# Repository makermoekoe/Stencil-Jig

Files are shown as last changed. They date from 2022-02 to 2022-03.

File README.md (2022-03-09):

# Stencil-Jig

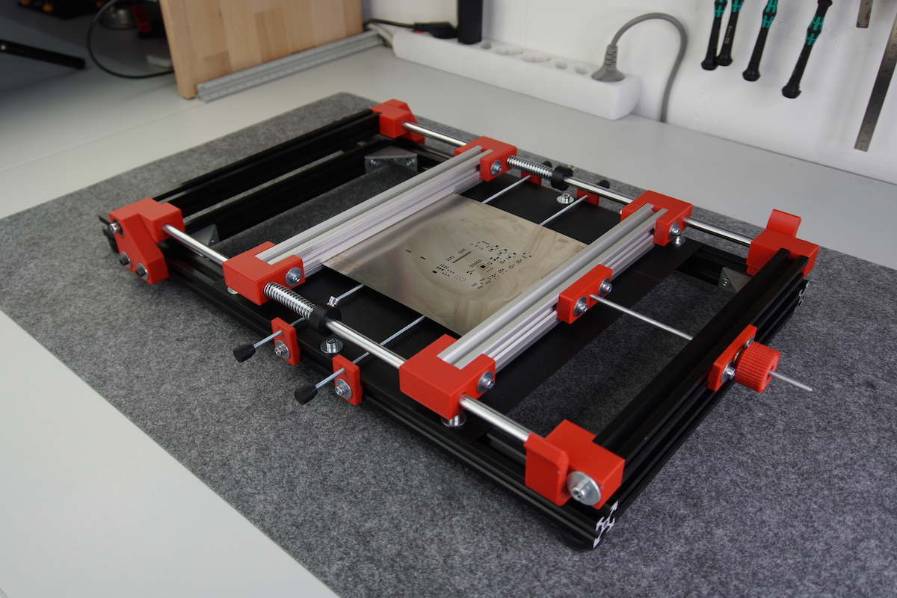
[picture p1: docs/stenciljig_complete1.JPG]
</a>
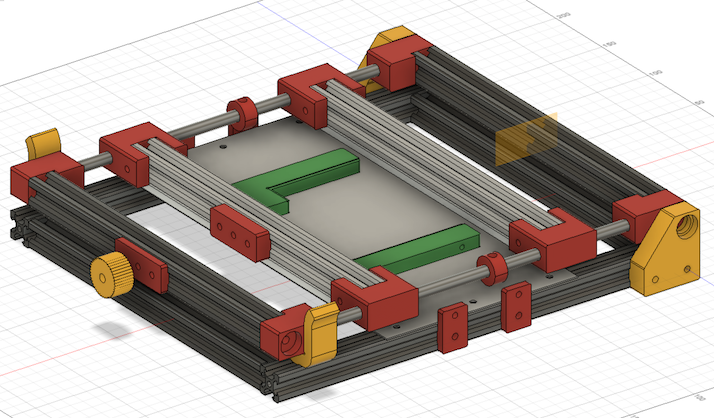
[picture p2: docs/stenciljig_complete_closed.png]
</a>
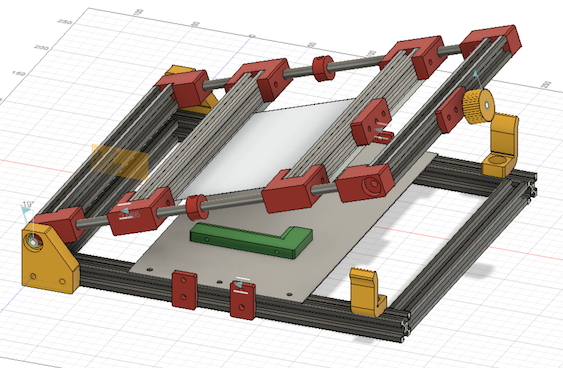
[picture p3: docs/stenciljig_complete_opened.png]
</a>

The Stencil-Jig is a simple DIY machine for PCB stenciling built with the Openbuilds v-slot system. Dealing with those stencils is always tricky, because they have to be aligned perfectly to get great soldering results. So far, I was always using these stencils with spare PCBs around the project PCB which are fixed in position with tape. As I am using these stencils quite often in the last time I was thinking about creating a simple jig for it - and here it is.

The stencils can be clamped into the Stencil-Jig with the inner v-slot extrusions. With all the adjustment screws on the sides and the front, the PCB and the stencil can be aligned easily to fit each other (at least this is the plan). The PCB holders are not yet the best option but they are working for now. If you have other ideas of how the PCB alignment could be done better then please let me know!

These built is inspired by two other DIY designs of Stencil printers/jigs/machines:

- Valera Perinski: https://www.thingiverse.com/thing:3429201
- Dengler Mechatronik: https://dengler-mechatronik.de/?p=560

## Assembling

I've created a detailed video about the assembly process of the StencilJig. There are notes in the video as well.

- video link here

## Extrusions

V-slot extrusions are probably not necessary here, because the v-bearings are not used. Nevertheless I have chosen them because of the availability and v-style of the slots in order to align 3D-printed parts with only one screw.

For this project you will need 5x 500mm 2020 extrusions which will be cut into these dimensions:

- 6x 250mm; width of the jig (it is probably 249,5mm, because I have just cut a 500mm extrusion in half)
- 2x 500mm; length of the jig (can be shortened later, so I leaved it as it is first)

## What to print

For the complete machine, as it is seen in the picture below, you'll need the following parts to be printed:

- 1x hinge_left.stl
- 1x hinge_right.stl
- 4x slide_mount.stl
- 4x slider.stl
- 2x slide_stopper.stl
- 2x alignment_guide.stl
- 1x screwstop_m4_incl.stl
- 1x screwstop_m4_knob.stl
- 1x knob_m4.stl
- 4x screwstop.stl
- 4x knob_m3.stl
- 1x pcb_mount_edge_1_6mm.stl
- 1x pcb_mount_straight_1_6mm.stl

## What you need

Except the 3D printed parts and the extrusions listed above you will also need the following parts:

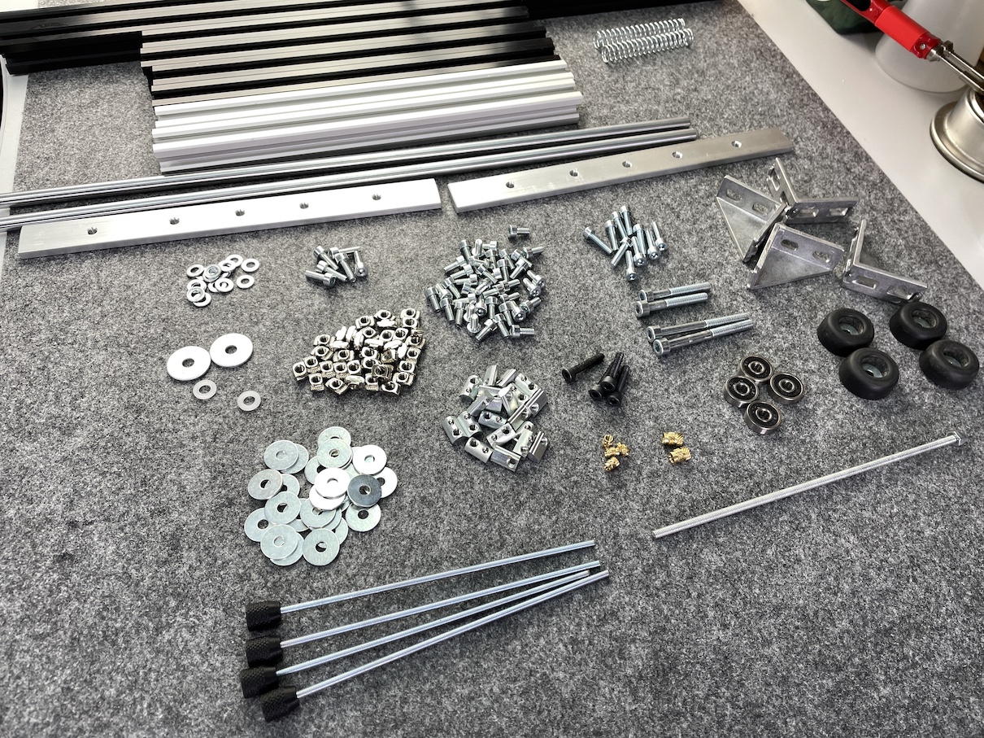
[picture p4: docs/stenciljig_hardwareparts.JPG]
</a>

- 2x 8mm stainless steel rod (length = length of the jig - 40mm)
- 4x 625RS bearings (16x5x5mm)
- 2x strong springs for the 8mm rod
- 4x M3 threaded rod ~100mm
- 1x M4 threaded rod ~100mm
- 1x steel plate 1mm (~290mmx250mm)
- 2x aluminium extrusion 5x20x220mm
- 4x extrusion corner 4040
- 4x M3 threaded insert
- 3x M4 threaded insert
- 40x M4 screw DIN 912 8mm
- 6x M4 screw DIN 912 12mm
- 10x M4 screw DIN 912 20mm
- 4x M4 screw DIN 912 25mm
- 2x M5 screw DIN 912 50mm
- 2x M5 screw DIN 912 30mm
- 60x M4 extrusion nuts
- 1x M4 self-locking nut
- Xx washers 4,3mm x 15mm
- 4x washers 5,3mm x 15mm
- 2x washers 5,3mm x 10mm polyamid
- (4x machine foots)

## Alignment guides

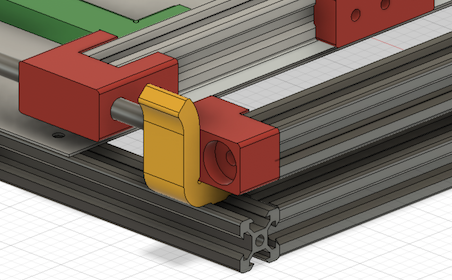
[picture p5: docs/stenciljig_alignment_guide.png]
</a>

The alignment guides are there to hold the upper part of the jig (including the stencil) during the stenceling process in place, so that it doesn't move to the left or right.

## TODOs

- Alignment guide: This part should be modified with two magnets facing against each other so that the top of jig will be pushed down once inserted in the alignment guide. This will keep the stencil down.
- The PCB holders should be optimized. At least they should be wider and on the same high as the PCB so that the stencil won't bent.
- Springs should be stronger. Or exchanging the springs with a tightener (knob as in the front) on the back?!

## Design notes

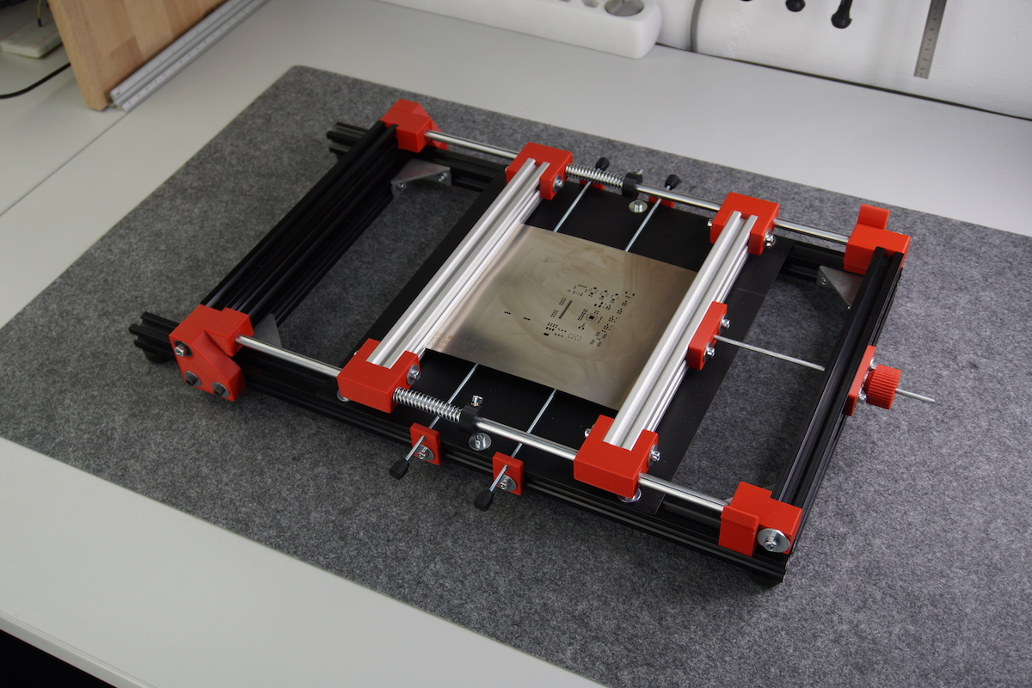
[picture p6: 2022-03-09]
docs/stenciljig_complete2.JPG

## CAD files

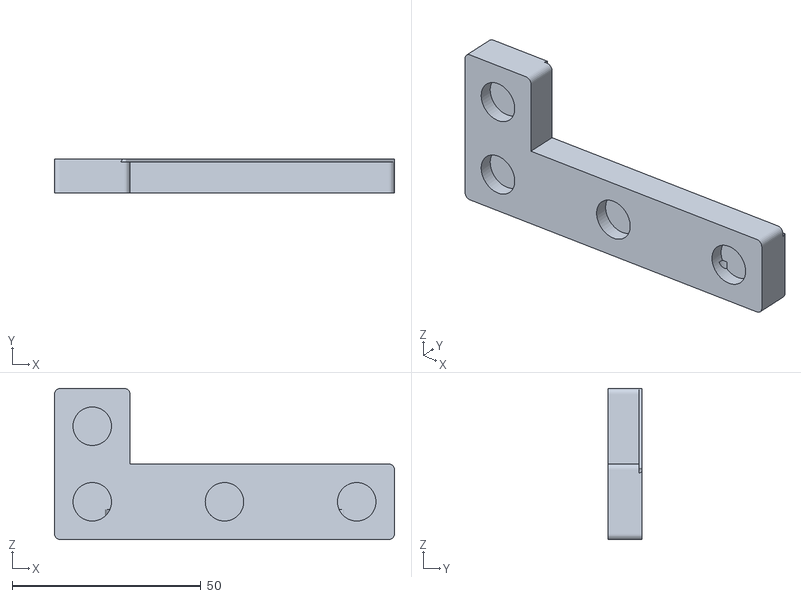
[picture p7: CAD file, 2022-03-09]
3d_files/pcb_mount_edge_1_6mm.stl
90.0 x 9.00 x 40.0

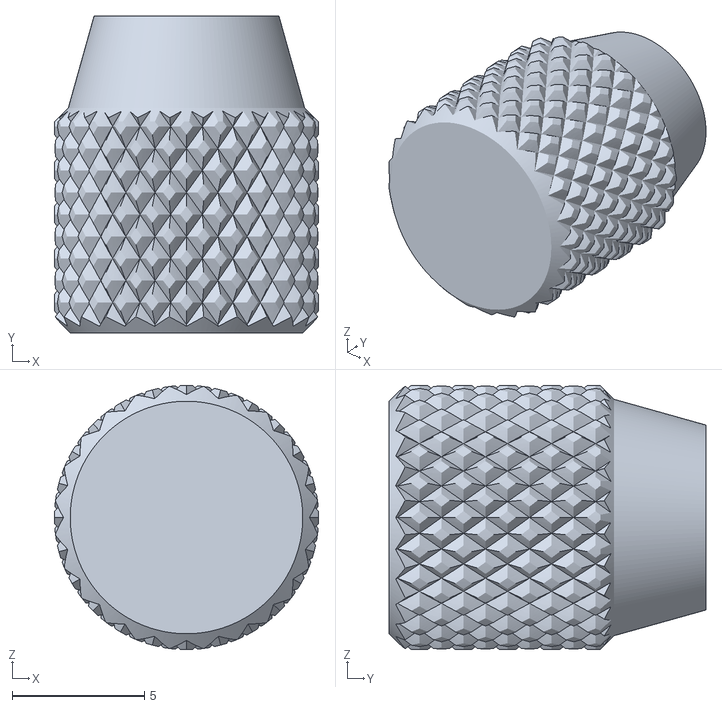
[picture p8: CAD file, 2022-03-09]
3d_files/knob_m3.stl
10.0 x 12.0 x 10.0

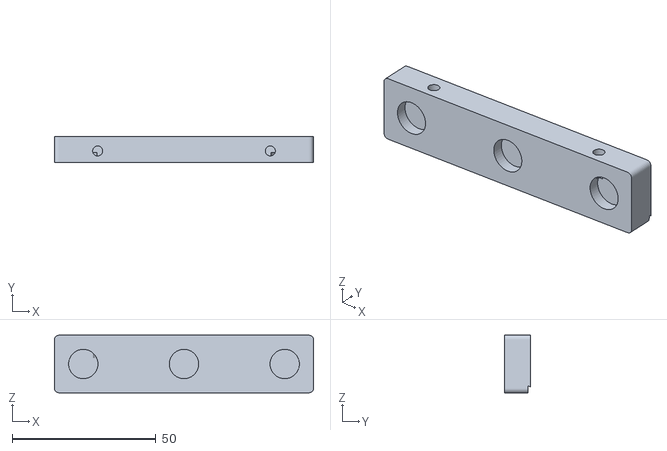
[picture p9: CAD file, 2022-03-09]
3d_files/pcb_mount_straight_1_6mm.stl
90.0 x 9.00 x 20.0

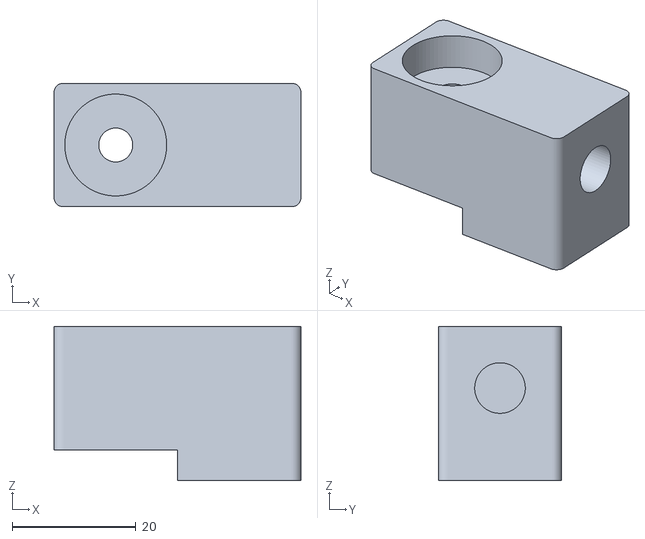
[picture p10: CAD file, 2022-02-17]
3d_files/slide_mount_front.stl
40.0 x 20.0 x 25.0

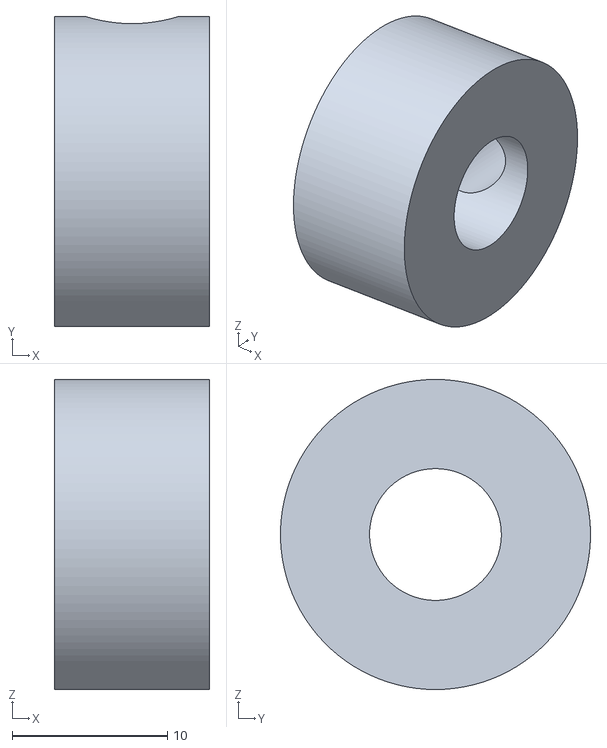
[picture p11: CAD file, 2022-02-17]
3d_files/slide_stopper.stl
10.0 x 20.0 x 20.0

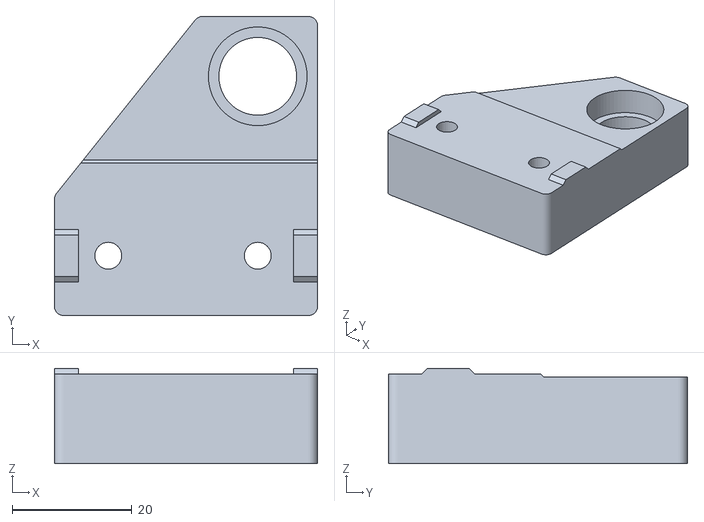
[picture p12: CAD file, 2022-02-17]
3d_files/hinge_left.stl
44.0 x 50.0 x 15.9

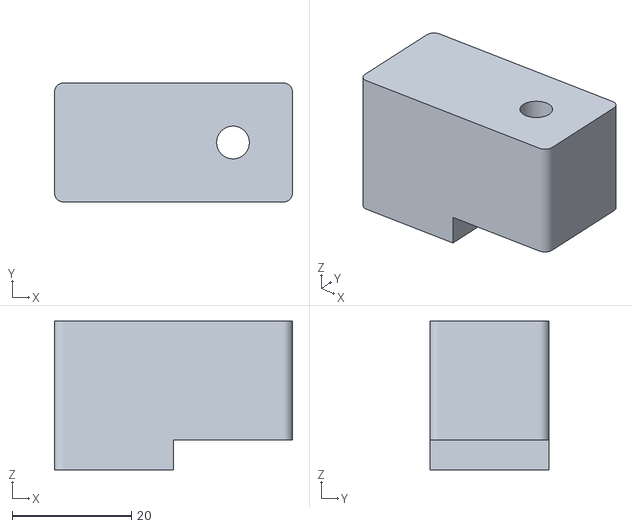
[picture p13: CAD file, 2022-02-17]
3d_files/slide_mount.stl
40.0 x 20.0 x 25.0

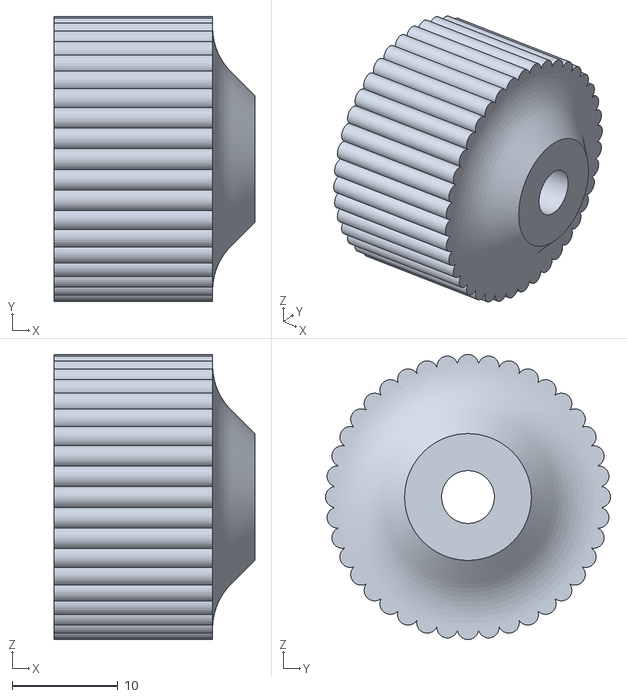
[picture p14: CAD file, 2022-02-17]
3d_files/knob_m4.stl
19.0 x 27.0 x 27.0

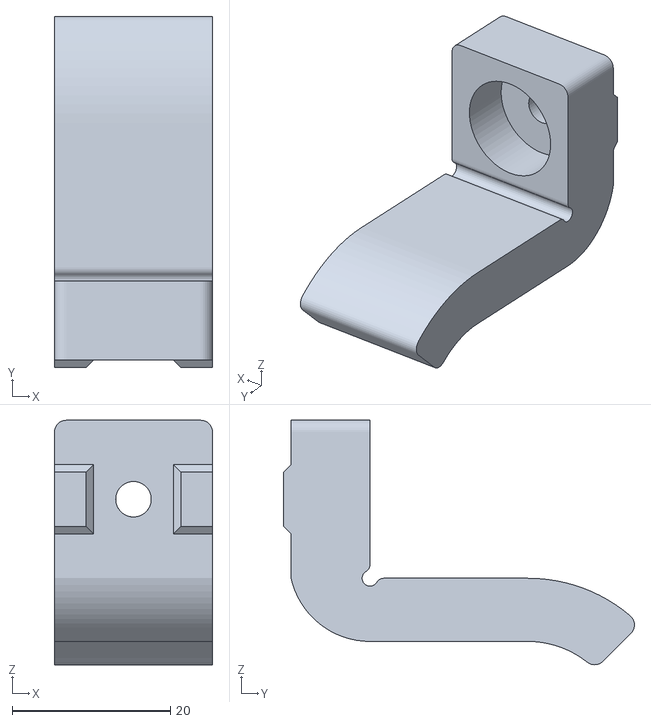
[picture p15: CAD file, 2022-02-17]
3d_files/alignment_guide.stl
20.0 x 44.4 x 31.0

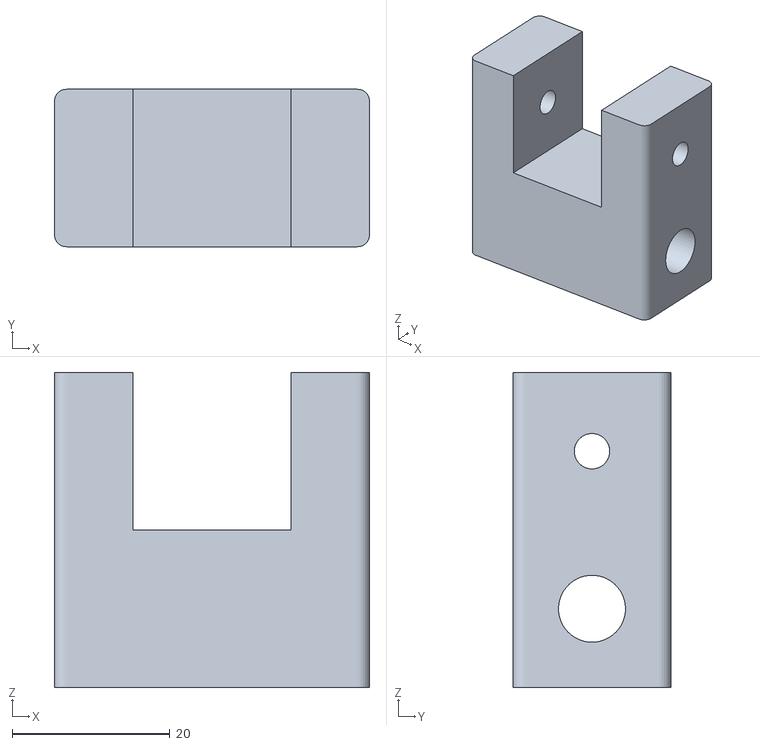
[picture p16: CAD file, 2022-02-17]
3d_files/slider.stl
40.0 x 20.0 x 40.0

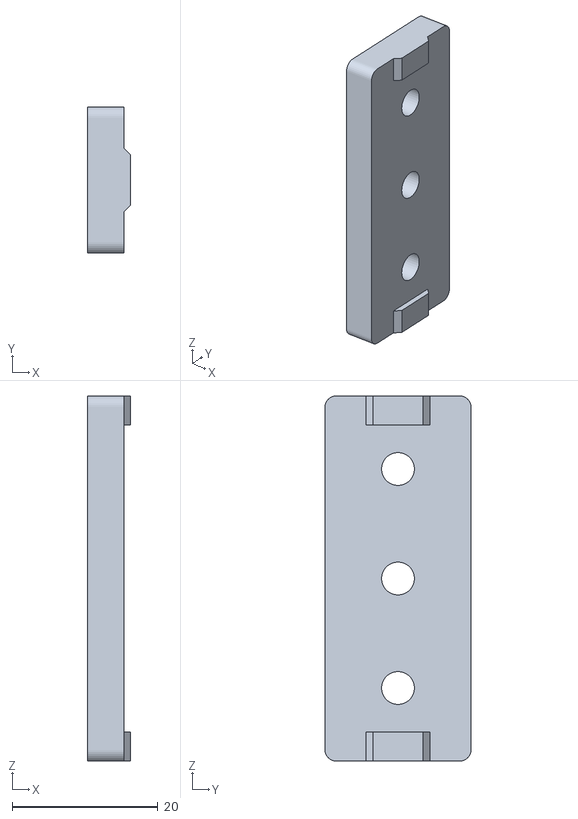
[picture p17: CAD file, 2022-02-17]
3d_files/screwstop_m4_knob.stl
5.95 x 20.0 x 50.0

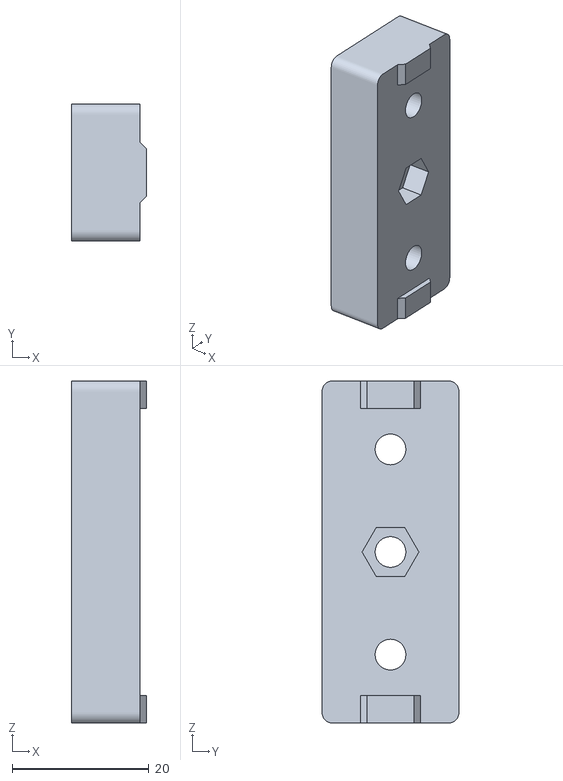
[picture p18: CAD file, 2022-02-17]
3d_files/screwstop_m4_incl.stl
10.9 x 20.0 x 50.0

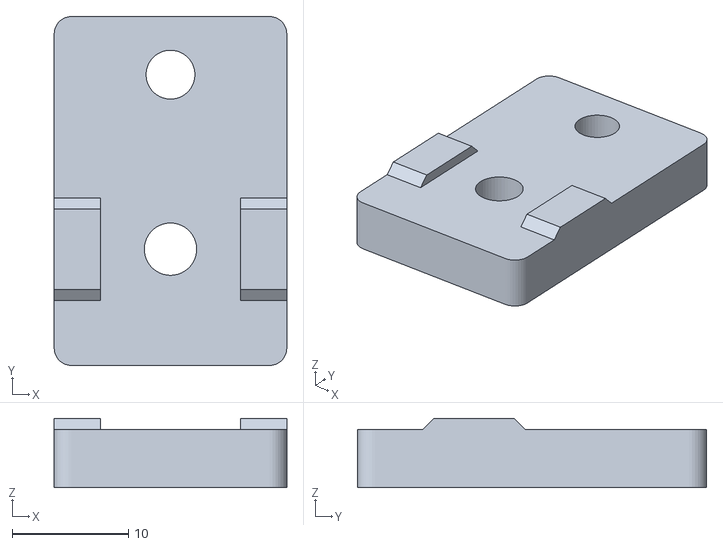
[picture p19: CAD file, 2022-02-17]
3d_files/screwstop.stl
20.0 x 30.0 x 5.95

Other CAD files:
3d_files/hinge_right.stl
3d_files/StencilJig v37.f3z

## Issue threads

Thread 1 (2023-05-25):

README inconsistencies

haimiko, 2023-05-25:
Problem with the descriptions in the non-3d printed parts

1. Extrusions don't add up.  Missing 2 and description confusing.
- 2x   5x20x220mm0 ?  Is this supposed to be 2 x   20x20x220  ?
- What about the other 2 top and bottom extrusions?

2. The 2 flat bars with 4 holes isn't in the list.  Dimensions?

mariuste, 2023-10-08:
I noticed the same issue. I looked at the fusion file an concluded the following sizes:
- 1 x steelplate: 290mm x 200mm (3d file is 290x150)
- 6 x aluminum extrusion 2020, 250mm
- 2 x aluminum extrusion 2020, 320mm
- 2 x 8mm rod 280mm

I will order the parts next month and try it out

joshenders, 2025-08-27:
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

How did it go?

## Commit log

2022-02-11 added first part bom
2022-02-17 added 3d files v1
    [alignment_guide.stl, hinge_left.stl, hinge_right.stl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]
2022-03-09 added 3d files and modified docs
    [knob_m3.stl, pcb_mount_edge_1_6mm.stl, pcb_mount_straight_1_6mm.stl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]
2022-10-10 added Fusion360 file
    [StencilJig v37.f3z]
